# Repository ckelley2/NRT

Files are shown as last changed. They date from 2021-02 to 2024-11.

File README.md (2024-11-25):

# NRT Design and Testing Documentation

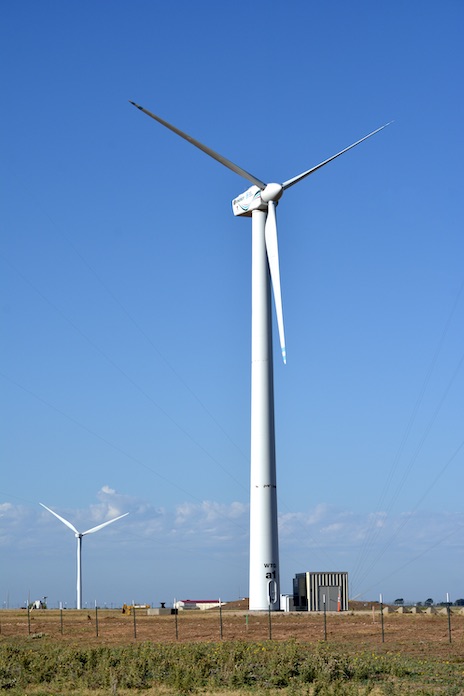
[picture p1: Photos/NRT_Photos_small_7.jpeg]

- National Rotor Testbed design documentation is contained in this repository
- [Field experiment](https://www.osti.gov/servlets/purl/1489535) is ongoing at Sandia/DOE SWiFT Facility, Lubbock, Texas
- Aerodynamic and instrumentation design by Sandia 
- Final structural design and manufacturing drawings were provided by Wetzel Wind Energy Services
- Oakridge National Laboratory 3D printed the NRT blade mold
- TPI Composites manufactured 4 NRT Blades
- Structural testing conducted at NREL

# Purpose
- To conduct wind turbine wake experiments relevant to megawatt scale turbines
- To be an open, well-documented, and highly instrumented wind turbine rotor design for model validation
- To demonstrate new blade technology

# [Aeroelastic Model](FAST_v7/)
- Modelled in [FAST version 7](https://www.nrel.gov/wind/nwtc/fastv7.html)
- Blade aerodynamics including chord, twist, and airfoil locations in aerodyn file [NRT_AD.ipt](FAST_v7/NRT_AD.ipt)
- Blade structural properites including edge, flap, tension, and torsional stiffness, mass moments of inertia, and mass distribution in each blade file [NRT_Blade1_as_built_balanced.dat](FAST_v7/NRT_Blade1_as_built_balanced.dat), [NRT_Blade2_as_built_balanced.dat](FAST_v7/NRT_Blade2_as_built_balanced.dat), [NRT_Blade3_as_built_balanced.dat](FAST_v7/NRT_Blade3_as_built_balanced.dat)
- Blade mass distribution updated to include ballast in balance boxes of each blade
- Airfoil lift, drag, and moment data from experimental wind tunnel testing by Somers
- Model will continue to be updated during ongoing NRT experiment
- Simple controller model, variable speed, variable pitch
- Please contact us for a detailed simulink model of the turbine controller
- Plotting scripts in matlab require [txt2mat](https://www.mathworks.com/matlabcentral/fileexchange/18430-txt2mat)

# Blade Instrumentation 
- Strain gages:
  - Micron Optics Fiber Optic OS3200
  - Spaced 45 degrees at root, high/low pressure side outboard
  - calibrated to measure aerodynamic bending moment
- Accelerometers:
  - Silicon Designs 2470
- Blade Temperature:
  - Micron Optics Fiber Optic OS4300
  - to compensate for thermal strain
- All three blades have same sensors  
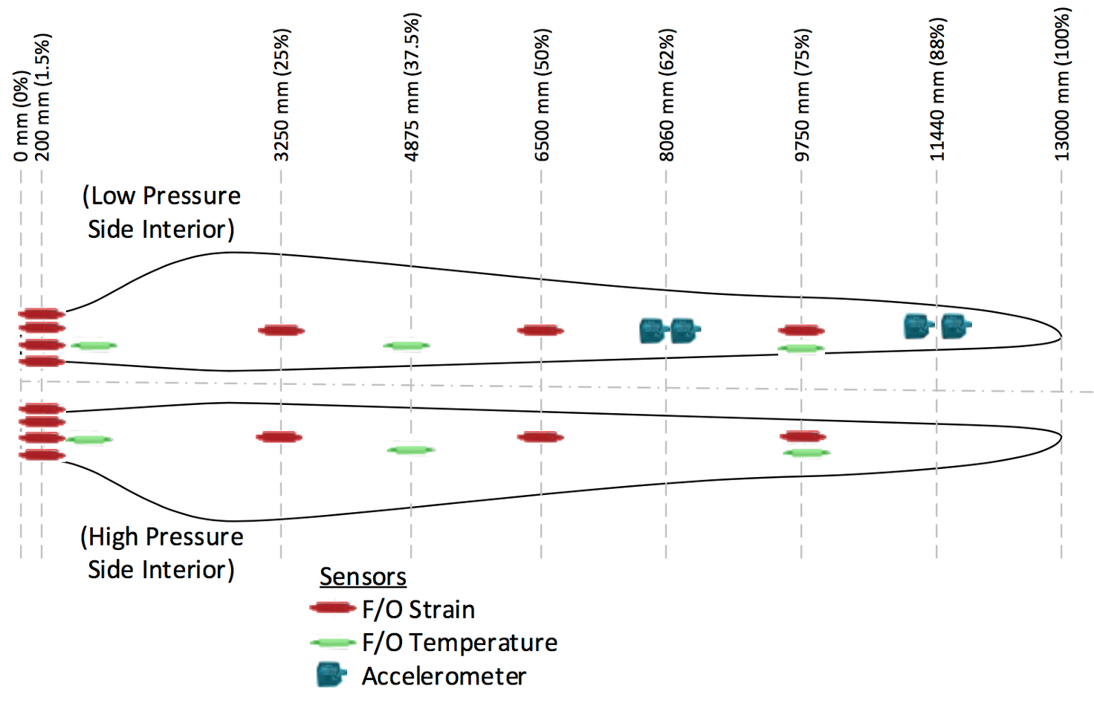
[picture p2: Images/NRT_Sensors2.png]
  

# Blade Properties
- Length: 13 m
- Blade Mass: 551 kg per blade, including balance box ballast 
- Blade Center of Gravity: 4.04 m from root
- Construction: Fiberglass spar and skin
- Surface Roughness (Painted, clean): Ra = 0.45 𝜇m (17 𝜇in), Rz = 2.57 𝜇m (101 𝜇in)

# Regions of Operation
- Region 2:   4-6.9 m/s, 25.9-43.6 rpm, TSR = 9
- Region 2.5: 6.9-11.4 m/s, 43.6-43.9 rpm
- Region 3:   11.4-20 m/s, 43.9 rpm   
  
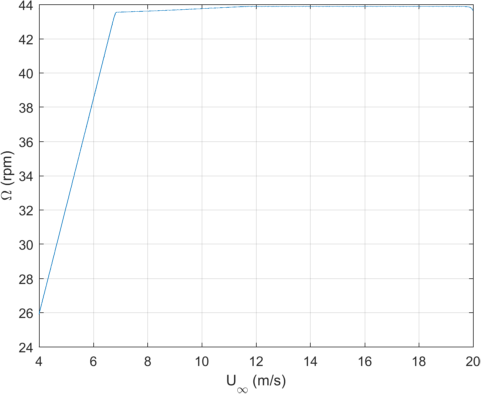
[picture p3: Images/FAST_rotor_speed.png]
 

# Aerodynamic Design
- [Technical Report](https://www.osti.gov/biblio/1346410-aerodynamic-design-national-rotor-testbed)
- Create scaled wake of GE 1.5sle (GE37c blade) by having the same axial induction, $a$, and dimensionless circulation, $\Gamma'$,  across the rotor normalized radius, $\frac{r}{R}$, in region 2
- NRT and GE rotor also have equal thrust coefficient $C_T$ and tip-speed-ratio $\lambda = 9$ in region 2
- [S825](https://www.nrel.gov/docs/fy05osti/36346.pdf) airfoil across outer 50% of rotor span
- [S814](https://wind.nrel.gov/airfoils/documents/S814_WTtest_OCR.pdf) airfoil at maximum chord, c = 1.5 m
- Airfoils operate at a lift coefficient of 0.6 in region 2  
- Overview of functional scaling [(.pdf)](Documents/NRT_Functional_Scaling.pdf)

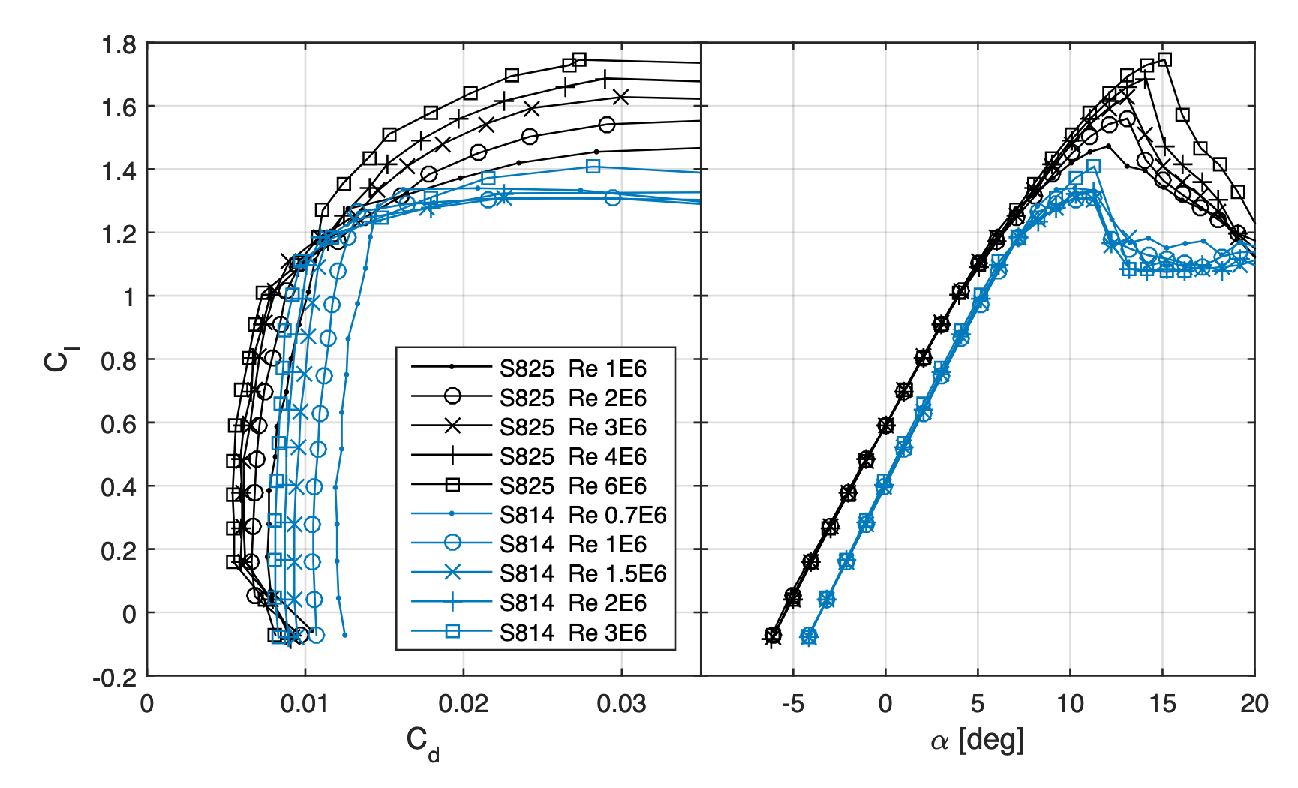
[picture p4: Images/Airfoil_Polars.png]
 <br/>

# Structural Design
- [Mass, Stiffness, and Modal Analysis Report (.pdf)](Structure/WEI%20169.03.06.001-B-Sandia%2013m%20Blade_Structural%20Analysis%20Summary.pdf)
- [Beam Properties (.xlsx)](Structure/169.05.02.001-B-Aero+Structure%20Design%20Summary.xlsx?raw=true)
- [Material Properties and Standards (.xlsx)](Structure/169.03.03.001-A_Sandia_13.0m%20Blade%20Materials%20and%20Test%20Standards_2016-02-....xlsx?raw=true)
- [3D CAD Models](Structure/3D%20CAD%20Models)
- [Manufacturing Drawings](Structure/Design%20Drawings)
- Note, the root plane was cut to add 0.5° of forward sweep to reduce nose down pitching moment about the blade pitch axis
- Initial structural design [report](https://www.osti.gov/biblio/1225852-nrt-rotor-structural-aeroelastic-analysis-preliminary-design-review) at Sandia in 2015, superseded by Wetzel structural design

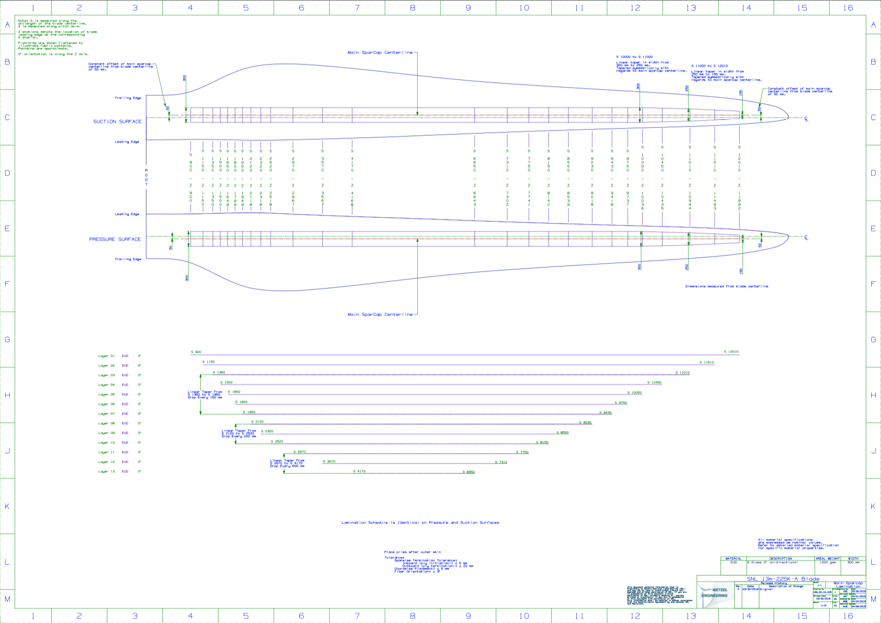
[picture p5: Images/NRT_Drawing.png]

  
# Static Blade Testing
- Conducted at NREL Structural Testing Lab
- [Test Report (.pdf)](Documents/NRT%20Blade%20Laboratory%20Structural%20Test%20Report.pdf)
- Proof Tests:
  - maximum and minimum edge loads
  - maximum and minimum flap loads
  - fatigue test in flap direction
  - ultimate flap load to failure
    
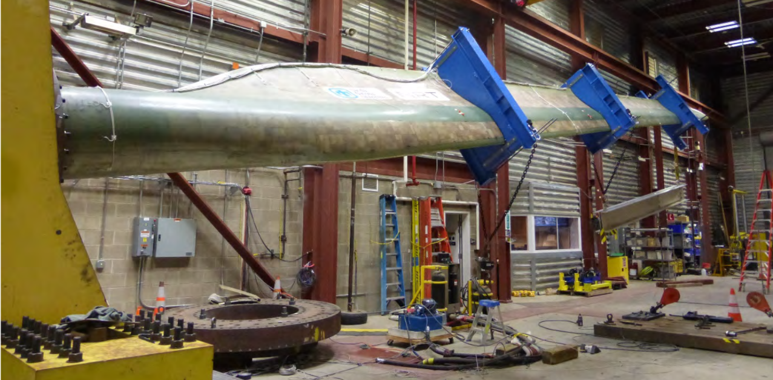
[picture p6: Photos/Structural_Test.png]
  

# Field Test
- Verify blade loading distribution creates scaled wake of GE 1.5 sle 
- Fine tune pitch setting to create scaled wake
- Fine tune torque constant to achieve $\lambda=9$
- See [technical report](https://www.osti.gov/servlets/purl/1489535) for description of tuning process
- Blade bending moment coefficients to achieve scaled wake (at reference air density of 1.225 $\textrm{kg/m}^3$) are as follows for discreet strain gage locations in thrust and edge directions
- Wake Management demonstration showing a combination of yaw, induction, and [dynamic induction](https://arc.aiaa.org/doi/abs/10.2514/6.2021-1182) control
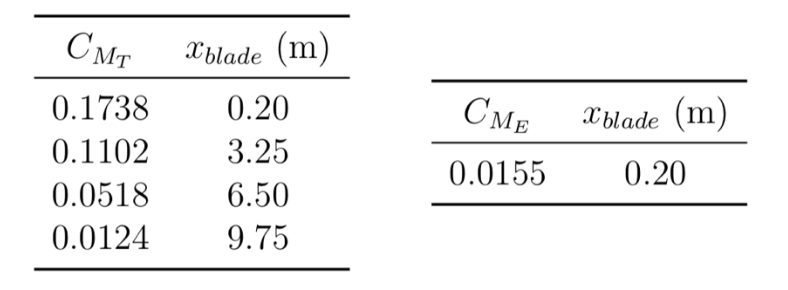
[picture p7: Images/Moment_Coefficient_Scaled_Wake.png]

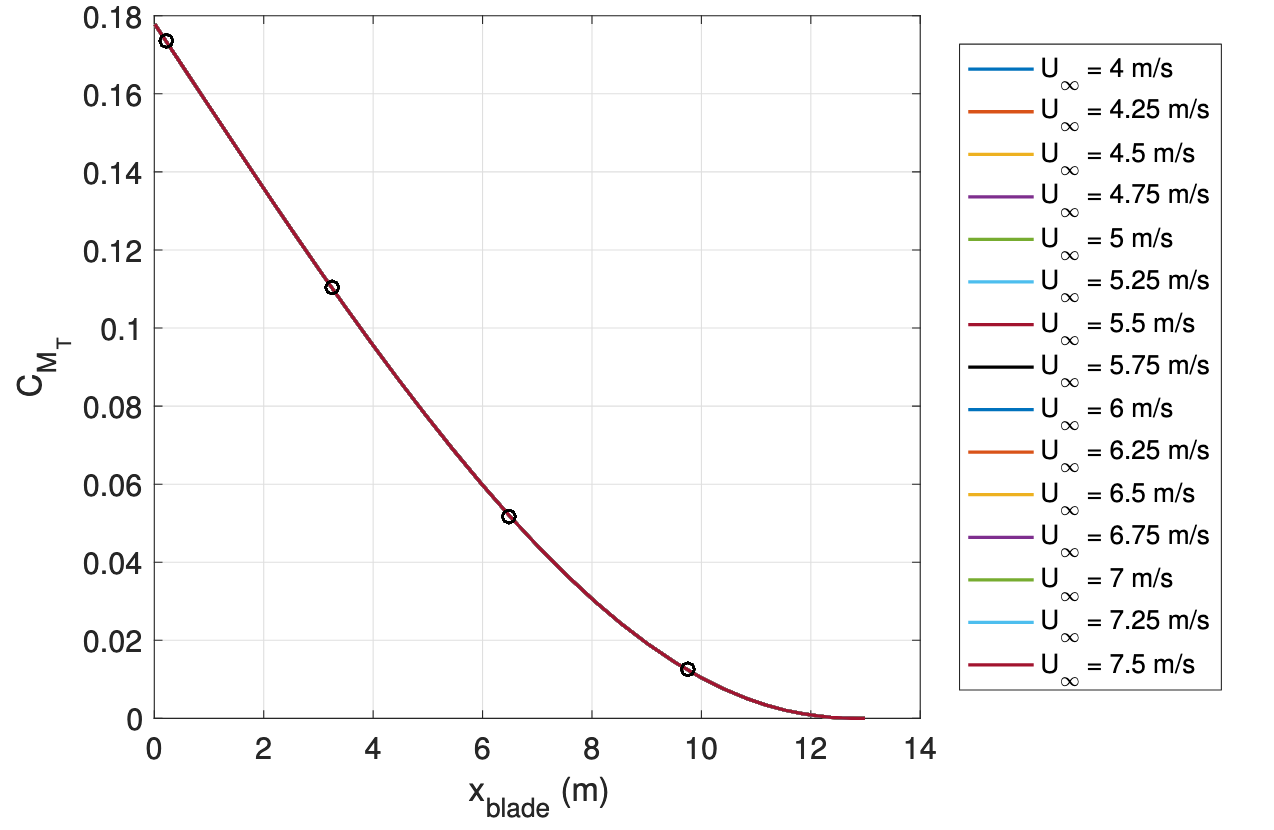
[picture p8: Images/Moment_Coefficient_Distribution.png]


# SWiFT Site Documentation
- [SWiFT Site Overview](https://energy.sandia.gov/programs/renewable-energy/wind-power/wind_plant_opt/)
- [Wind Resource Assessment and Characterization](https://www.osti.gov/biblio/1237403-swift-site-atmospheric-characterization)

# Point of Contact
Chris Kelley  
clkell@sandia.gov

# References
C. Kelley, "Aerodynamic Design of the National Rotor Testbed," Sandia National Laboratories Technical Report, [SAND2015-8989](https://www.osti.gov/biblio/1346410-aerodynamic-design-national-rotor-testbed).  

C. Kelley, B. Naughton, "NRT Design Verification Test Plan," Sandia National Laboratories Technical Report, [SAND2018-14254](https://www.osti.gov/biblio/1346410-aerodynamic-design-national-rotor-testbed).  

C. Kelley, "National Rotor Testbed Overview for DOE Science Panel," Project Presentation, [SAND2017-4446PE](https://www.osti.gov/servlets/purl/1431697).

B. Ennis, J. Paquette, "NRT Rotor Structural/Aeroelastic Analysis for the Preliminary Design Review," Sandia National Laboratories Technical Report, [SAND2015-9358](https://www.osti.gov/biblio/1225852-nrt-rotor-structural-aeroelastic-analysis-preliminary-design-review)

# Copyright
Copyright 2020 National Technology & Engineering Solutions of Sandia, 
LLC (NTESS). Under the terms of Contract DE-NA0003525 with NTESS, the U.S. 
Government retains certain rights.
 
NRT design documentation is distributed in the hope that it will be useful, but without any 
warranty; without even the implied warranty of merchantability or fitness for a 
particular purpose.

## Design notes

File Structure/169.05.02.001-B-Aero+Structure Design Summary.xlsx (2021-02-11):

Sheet: COVER
 | Sandia 13m BLADE AERO-STRUCTURE DESIGN SUMMARY
 | Document Number: |  | 169.05.02.001
 | Document Release Version: |  | B
 | Release Date: |  | 2016-04-26
 | Client: |  | Sandia National Laboratories
 | PO Number: |  | 42389
 | Agreement Date: |  | 1322724 Rev.11
 | Task: |  | 3B. Detail Structural Design
 | Client POC: |  | Josh Paquette
 | Consultant PI: |  | Dr. Kyle K. Wetzel
 | Document Approval |  |  | Name | Date
 | Curent Release Author: |  |  | Alejandra S. Escalera | 2016-04-21
 |  |  |  | (ase@WetzelEngineering.com)
 | Current Release Checked By: |  |  | Alex R. Tran | 2016-04-22
 | Current Release Approved By: |  |  | Kyle K. Wetzek | 2016-Apr-23
 | REVISION HISTORY
 | Version | Release Date | Author |  | Changes
 | A | 2016-03-09 | Alejandra S. Escalera |  | Original
 | B | 2016-04-22 | Alejandra S. Escalera |  | Updated after completion of task 3.C
Wetzel Engineering, Inc. ● 3914 Gattis School Road, Suite 103 ● Round Rock, TX 78664 ● U.S.A. 512-989-9194 ● info@WetzelEngineering.com ● www.WetzelEngineering.com
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

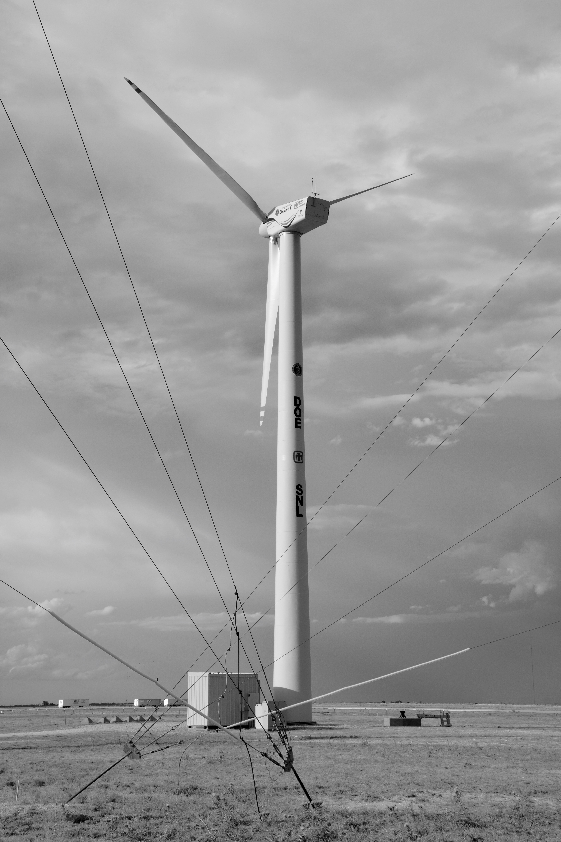
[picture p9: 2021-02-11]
Photos/NRT_Photos_4.jpeg

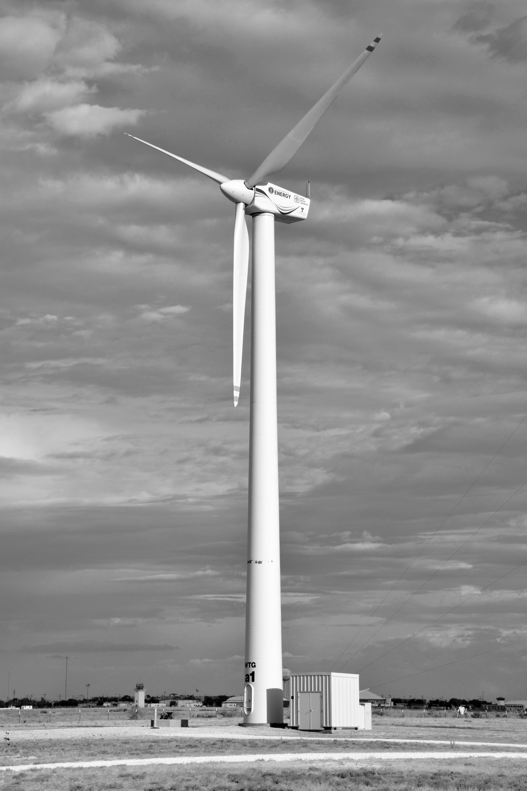
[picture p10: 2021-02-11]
Photos/NRT_Photos_2.jpeg

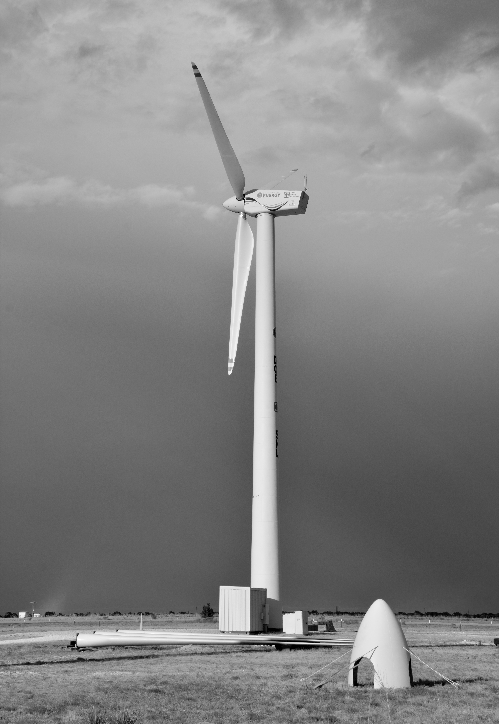
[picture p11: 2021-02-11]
Photos/NRT_Photos_5.jpeg

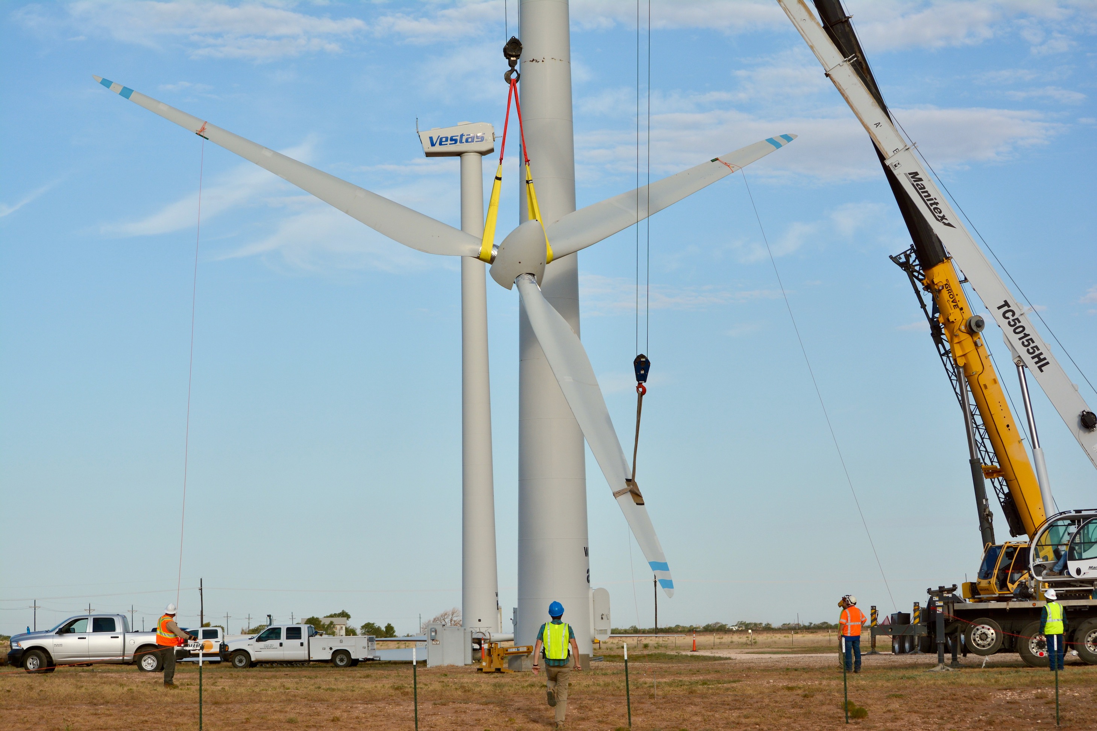
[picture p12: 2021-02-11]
Photos/NRT_Photos_small_1.jpeg

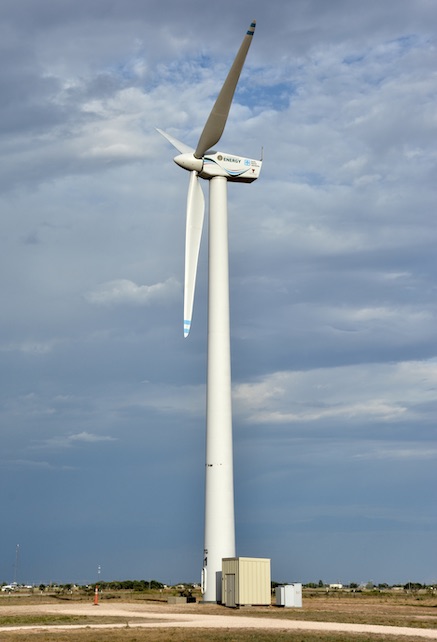
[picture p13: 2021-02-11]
Photos/NRT_Photos_small_3.jpeg

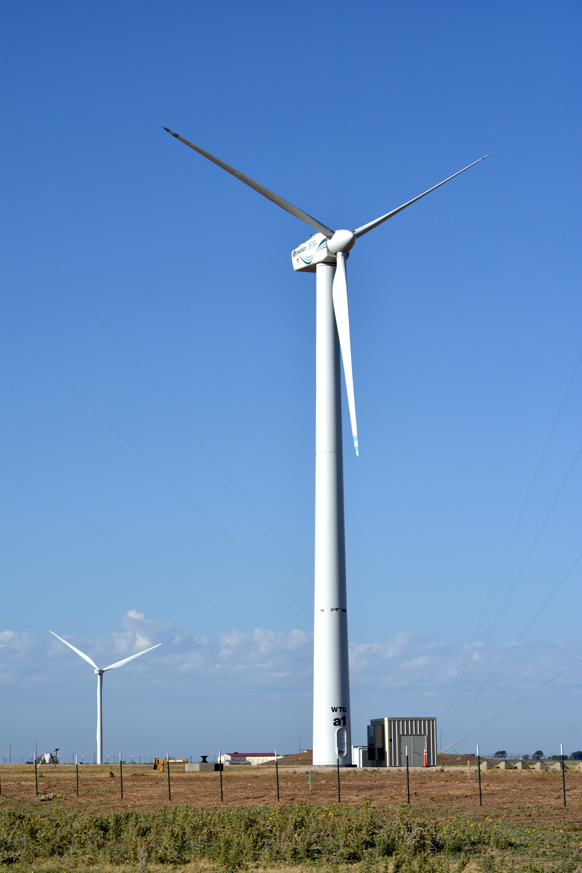
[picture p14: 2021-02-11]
Photos/NRT_Photos_7.jpeg

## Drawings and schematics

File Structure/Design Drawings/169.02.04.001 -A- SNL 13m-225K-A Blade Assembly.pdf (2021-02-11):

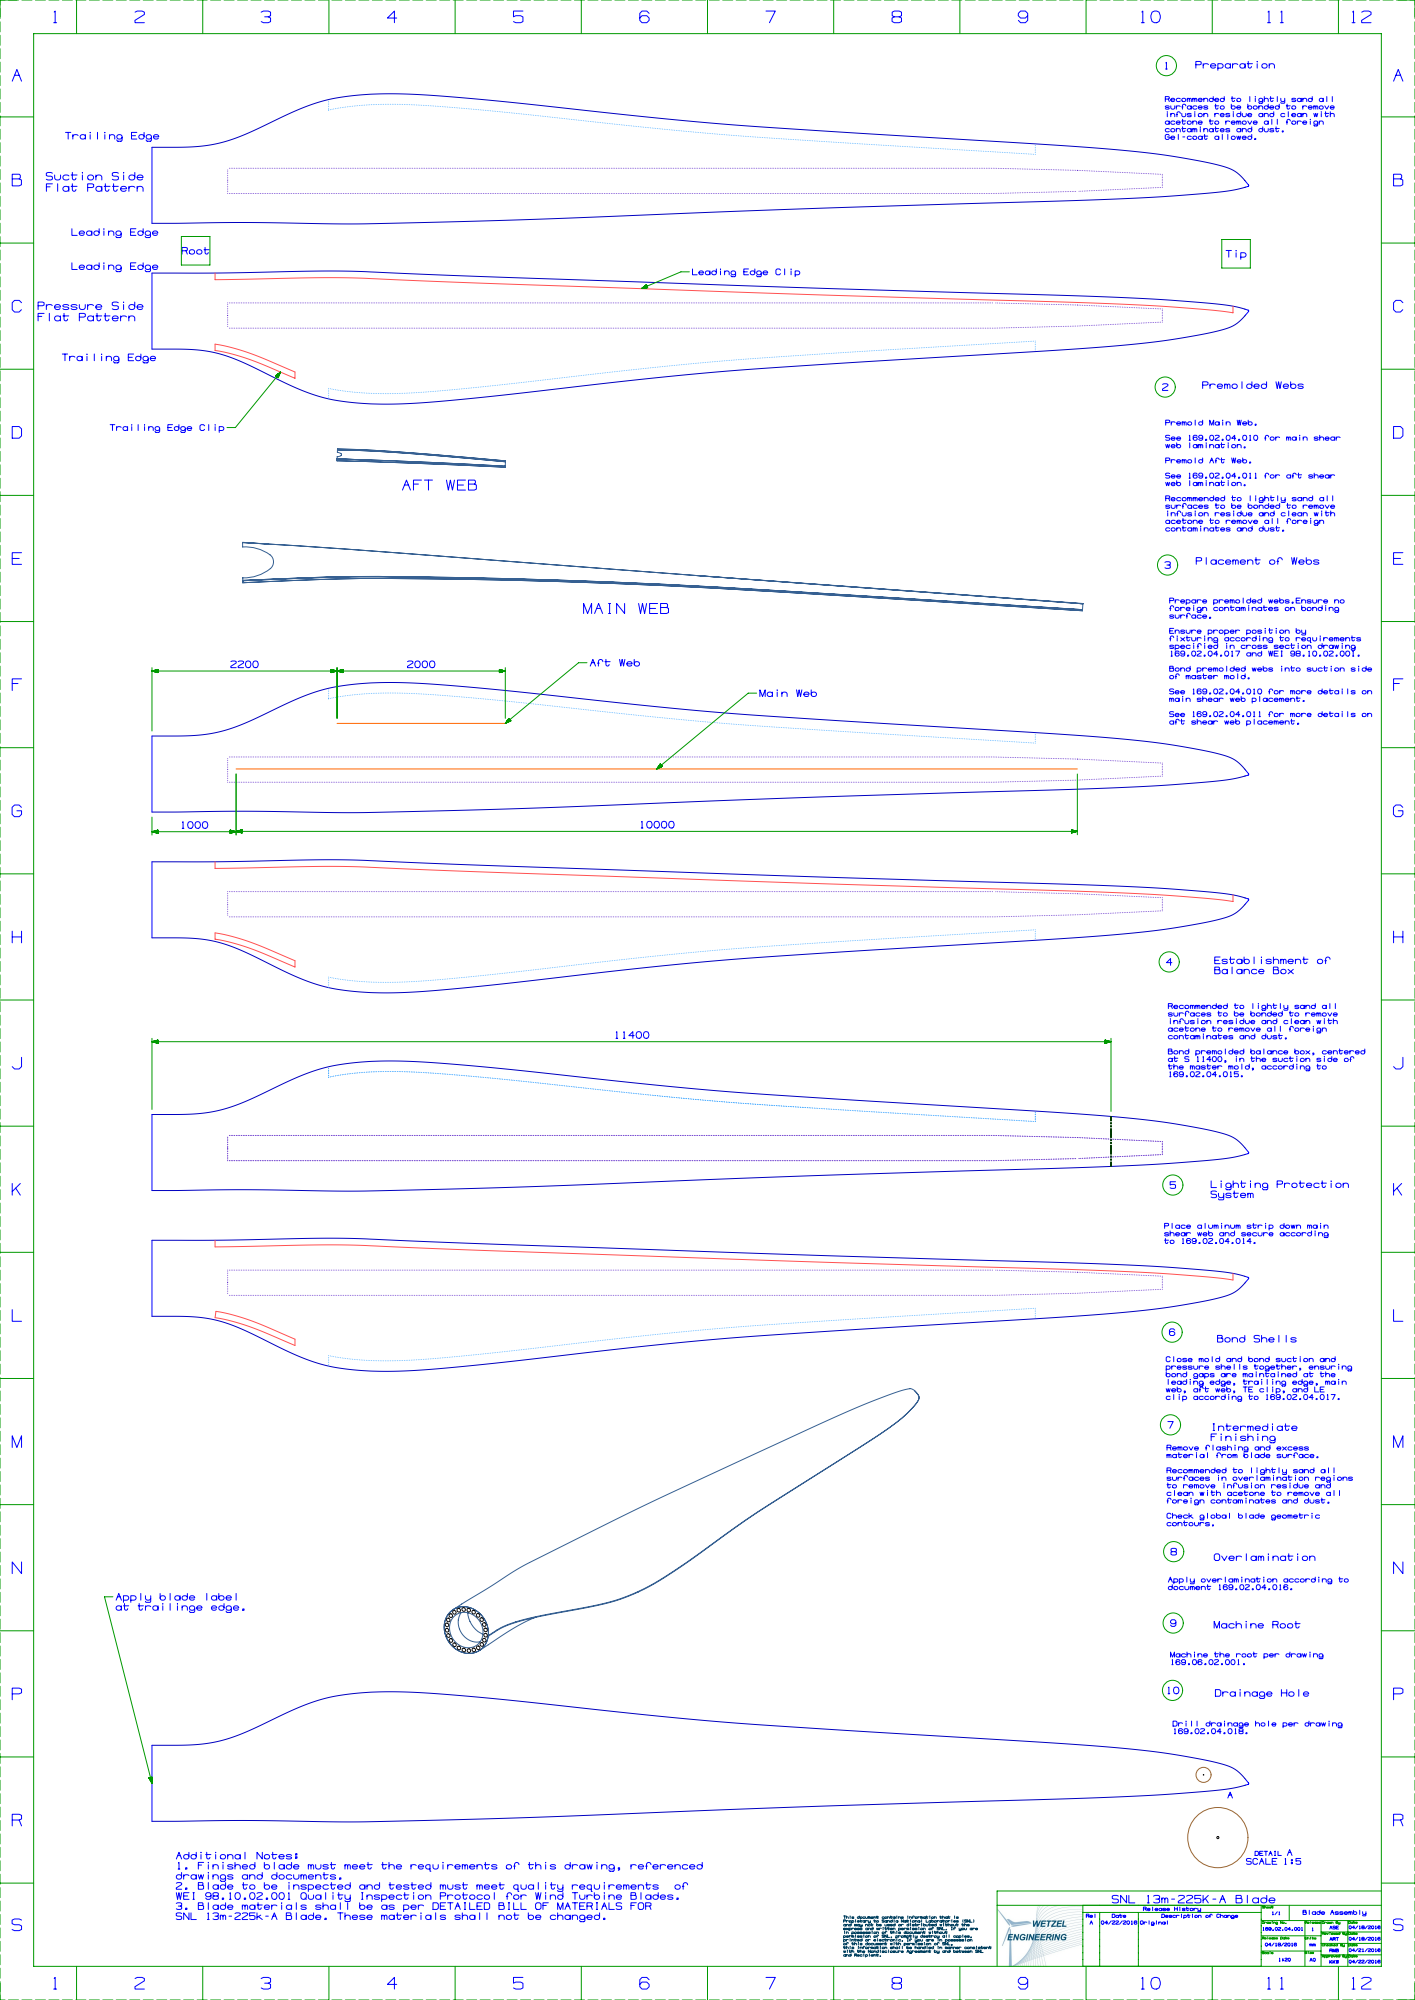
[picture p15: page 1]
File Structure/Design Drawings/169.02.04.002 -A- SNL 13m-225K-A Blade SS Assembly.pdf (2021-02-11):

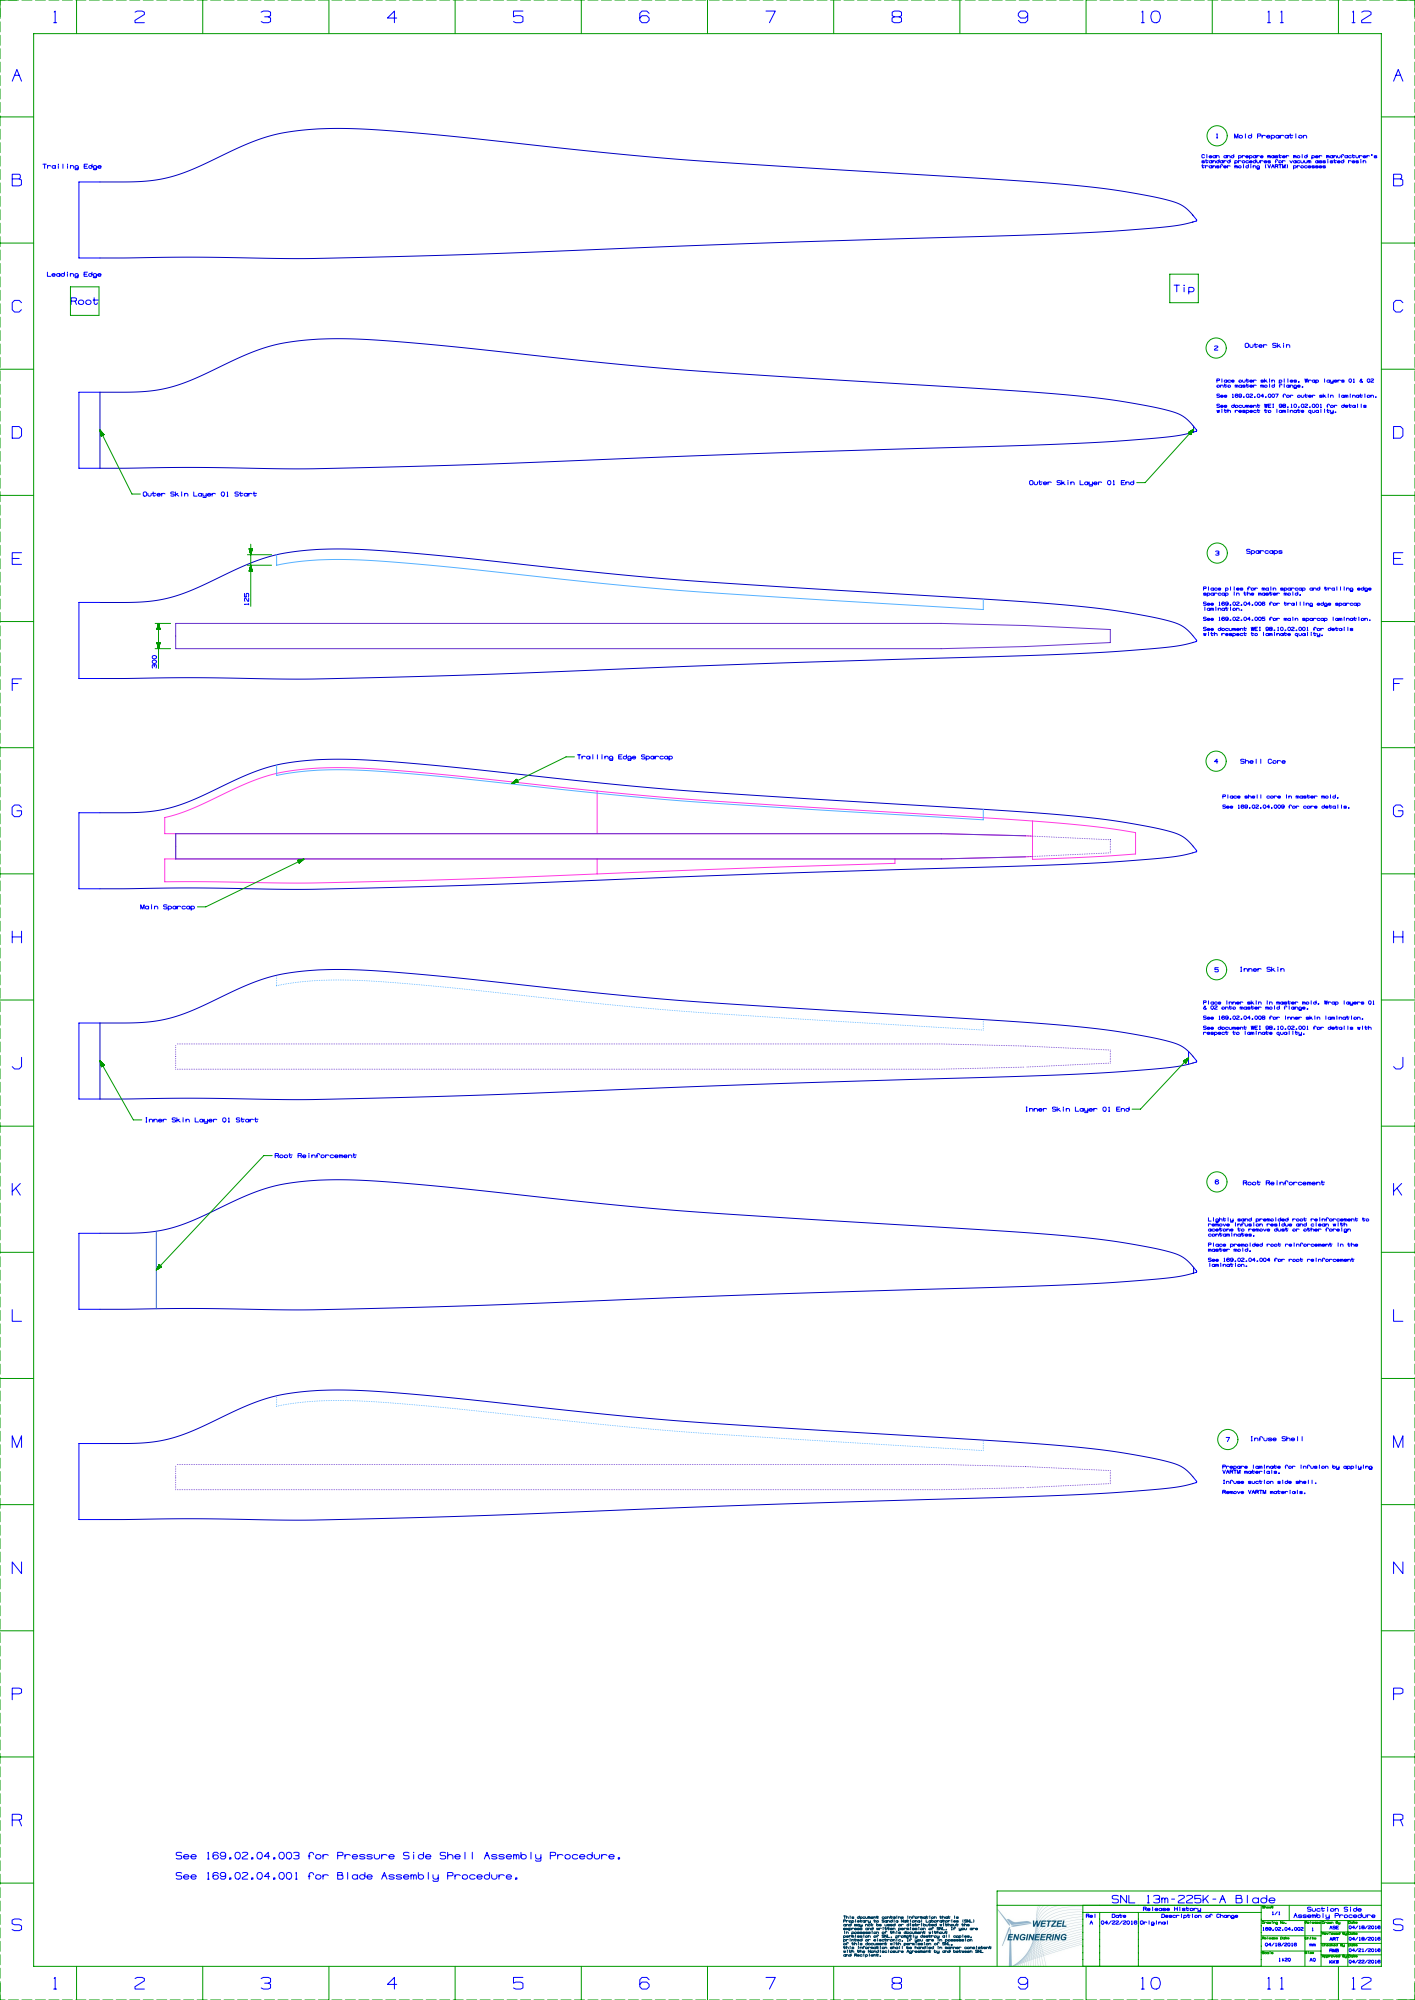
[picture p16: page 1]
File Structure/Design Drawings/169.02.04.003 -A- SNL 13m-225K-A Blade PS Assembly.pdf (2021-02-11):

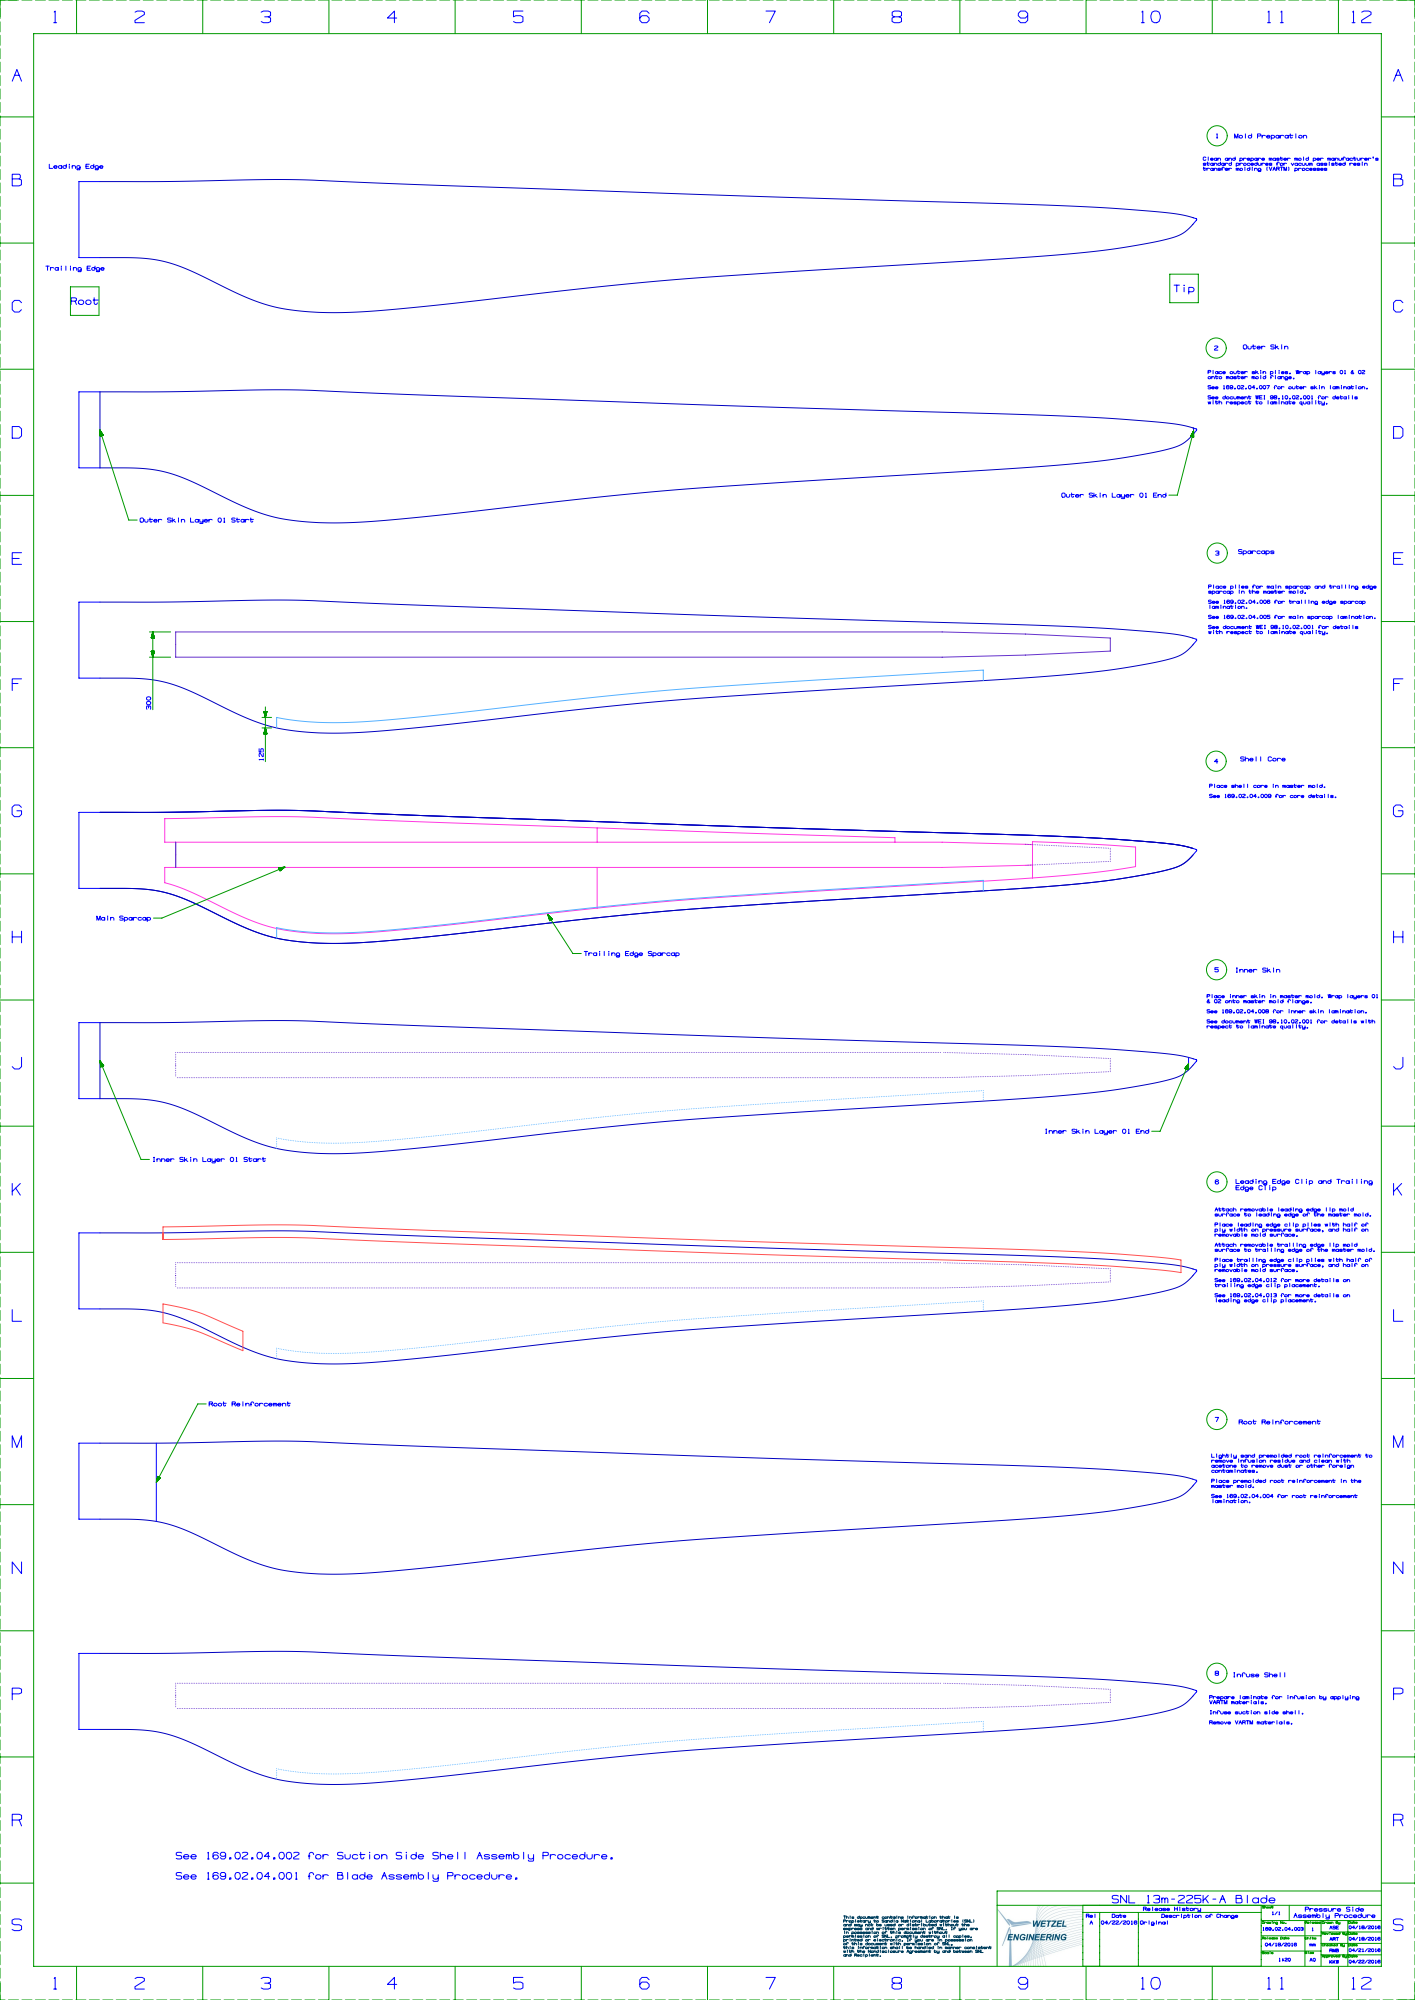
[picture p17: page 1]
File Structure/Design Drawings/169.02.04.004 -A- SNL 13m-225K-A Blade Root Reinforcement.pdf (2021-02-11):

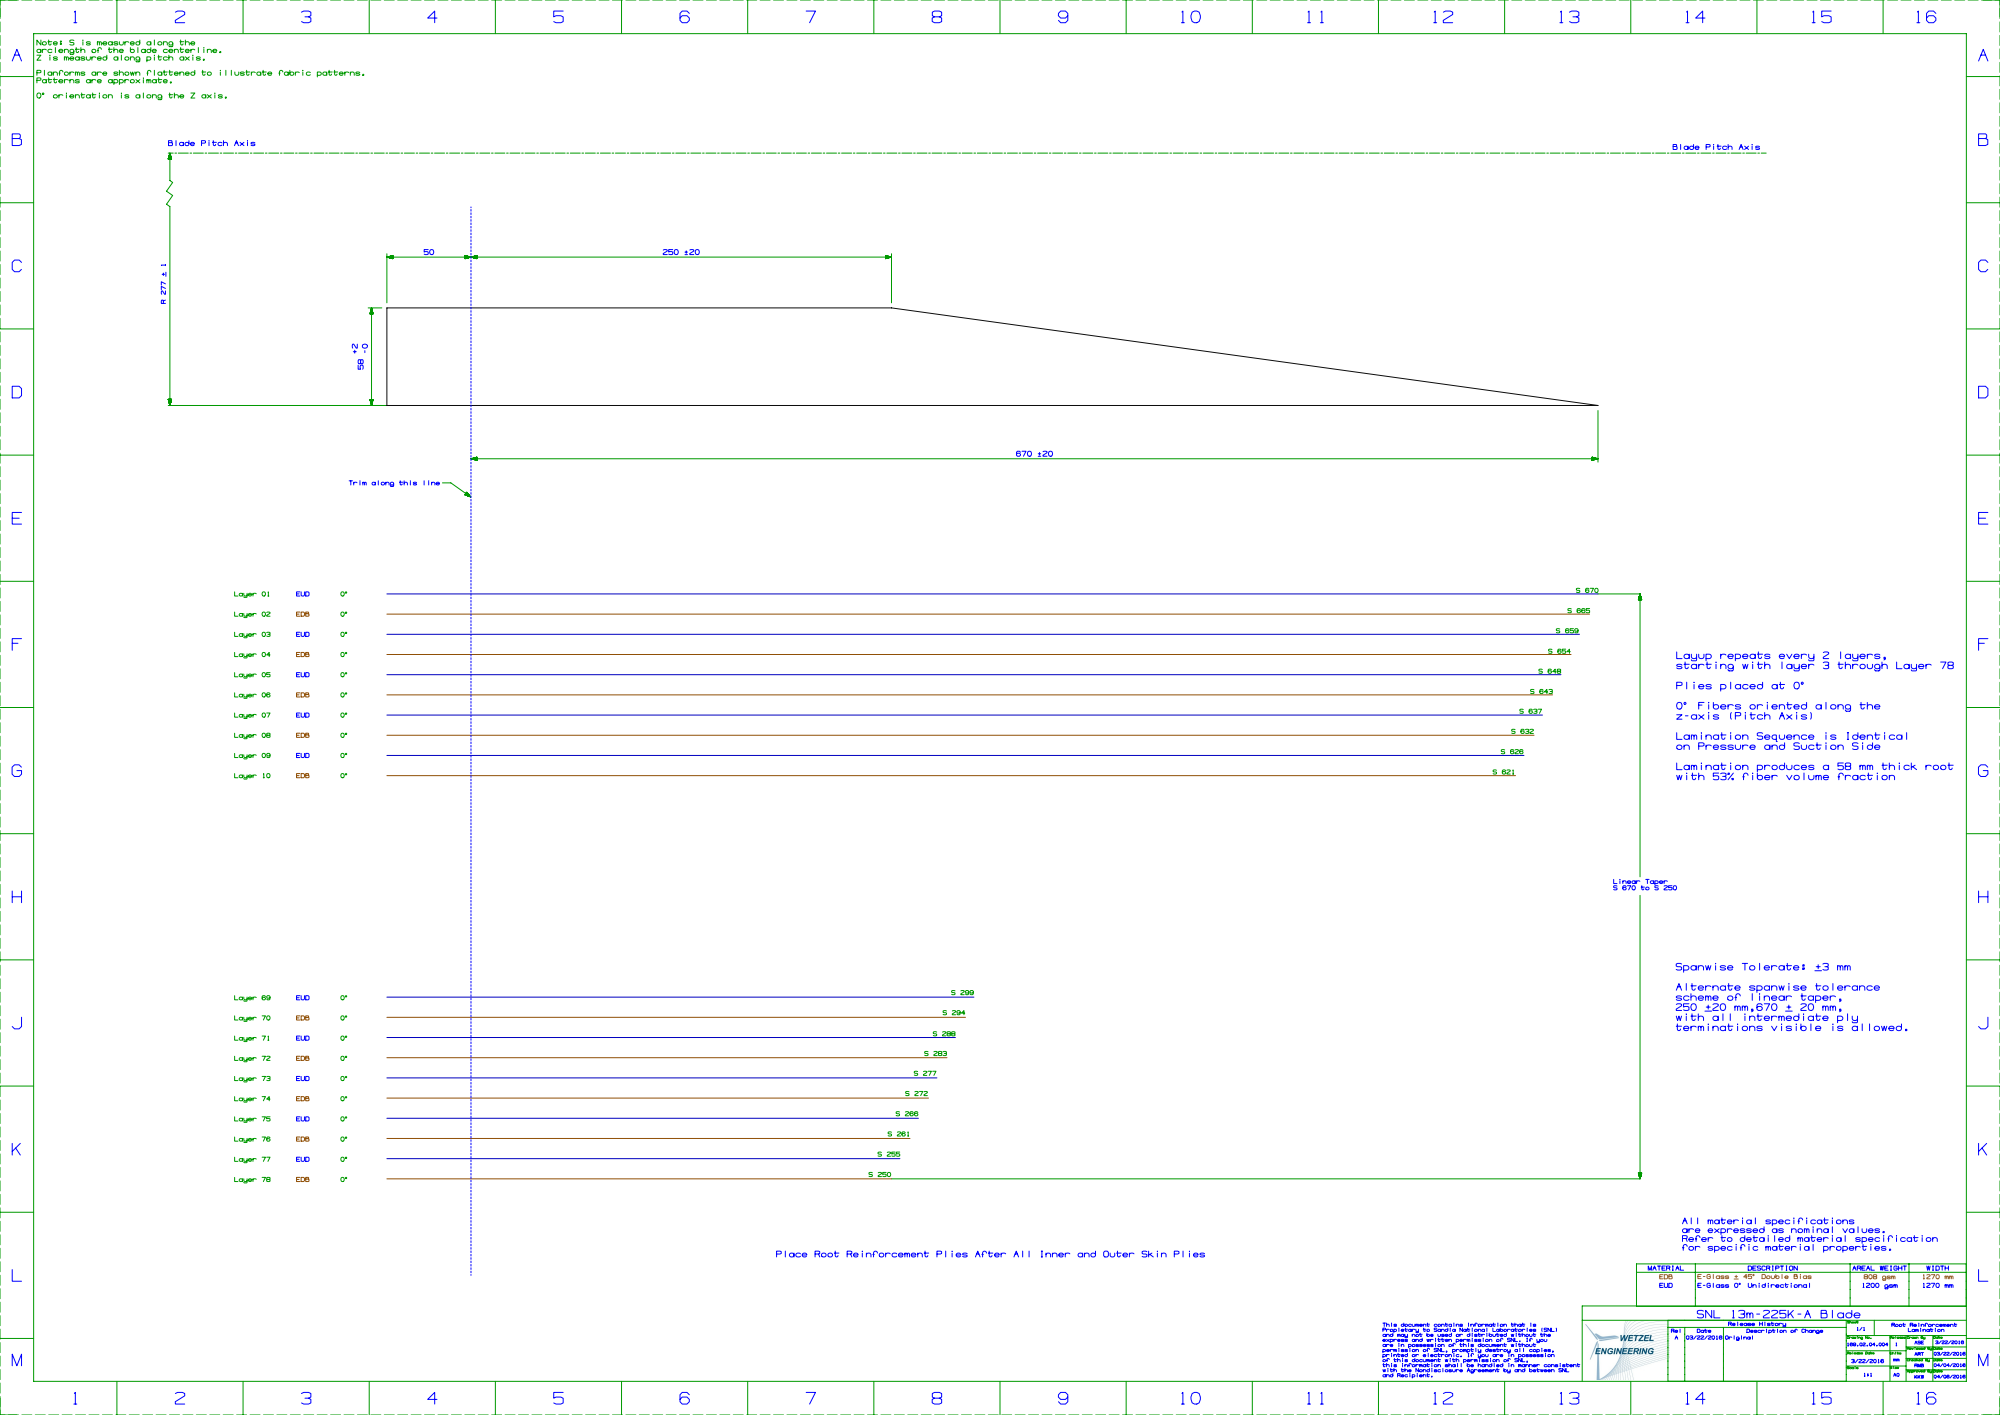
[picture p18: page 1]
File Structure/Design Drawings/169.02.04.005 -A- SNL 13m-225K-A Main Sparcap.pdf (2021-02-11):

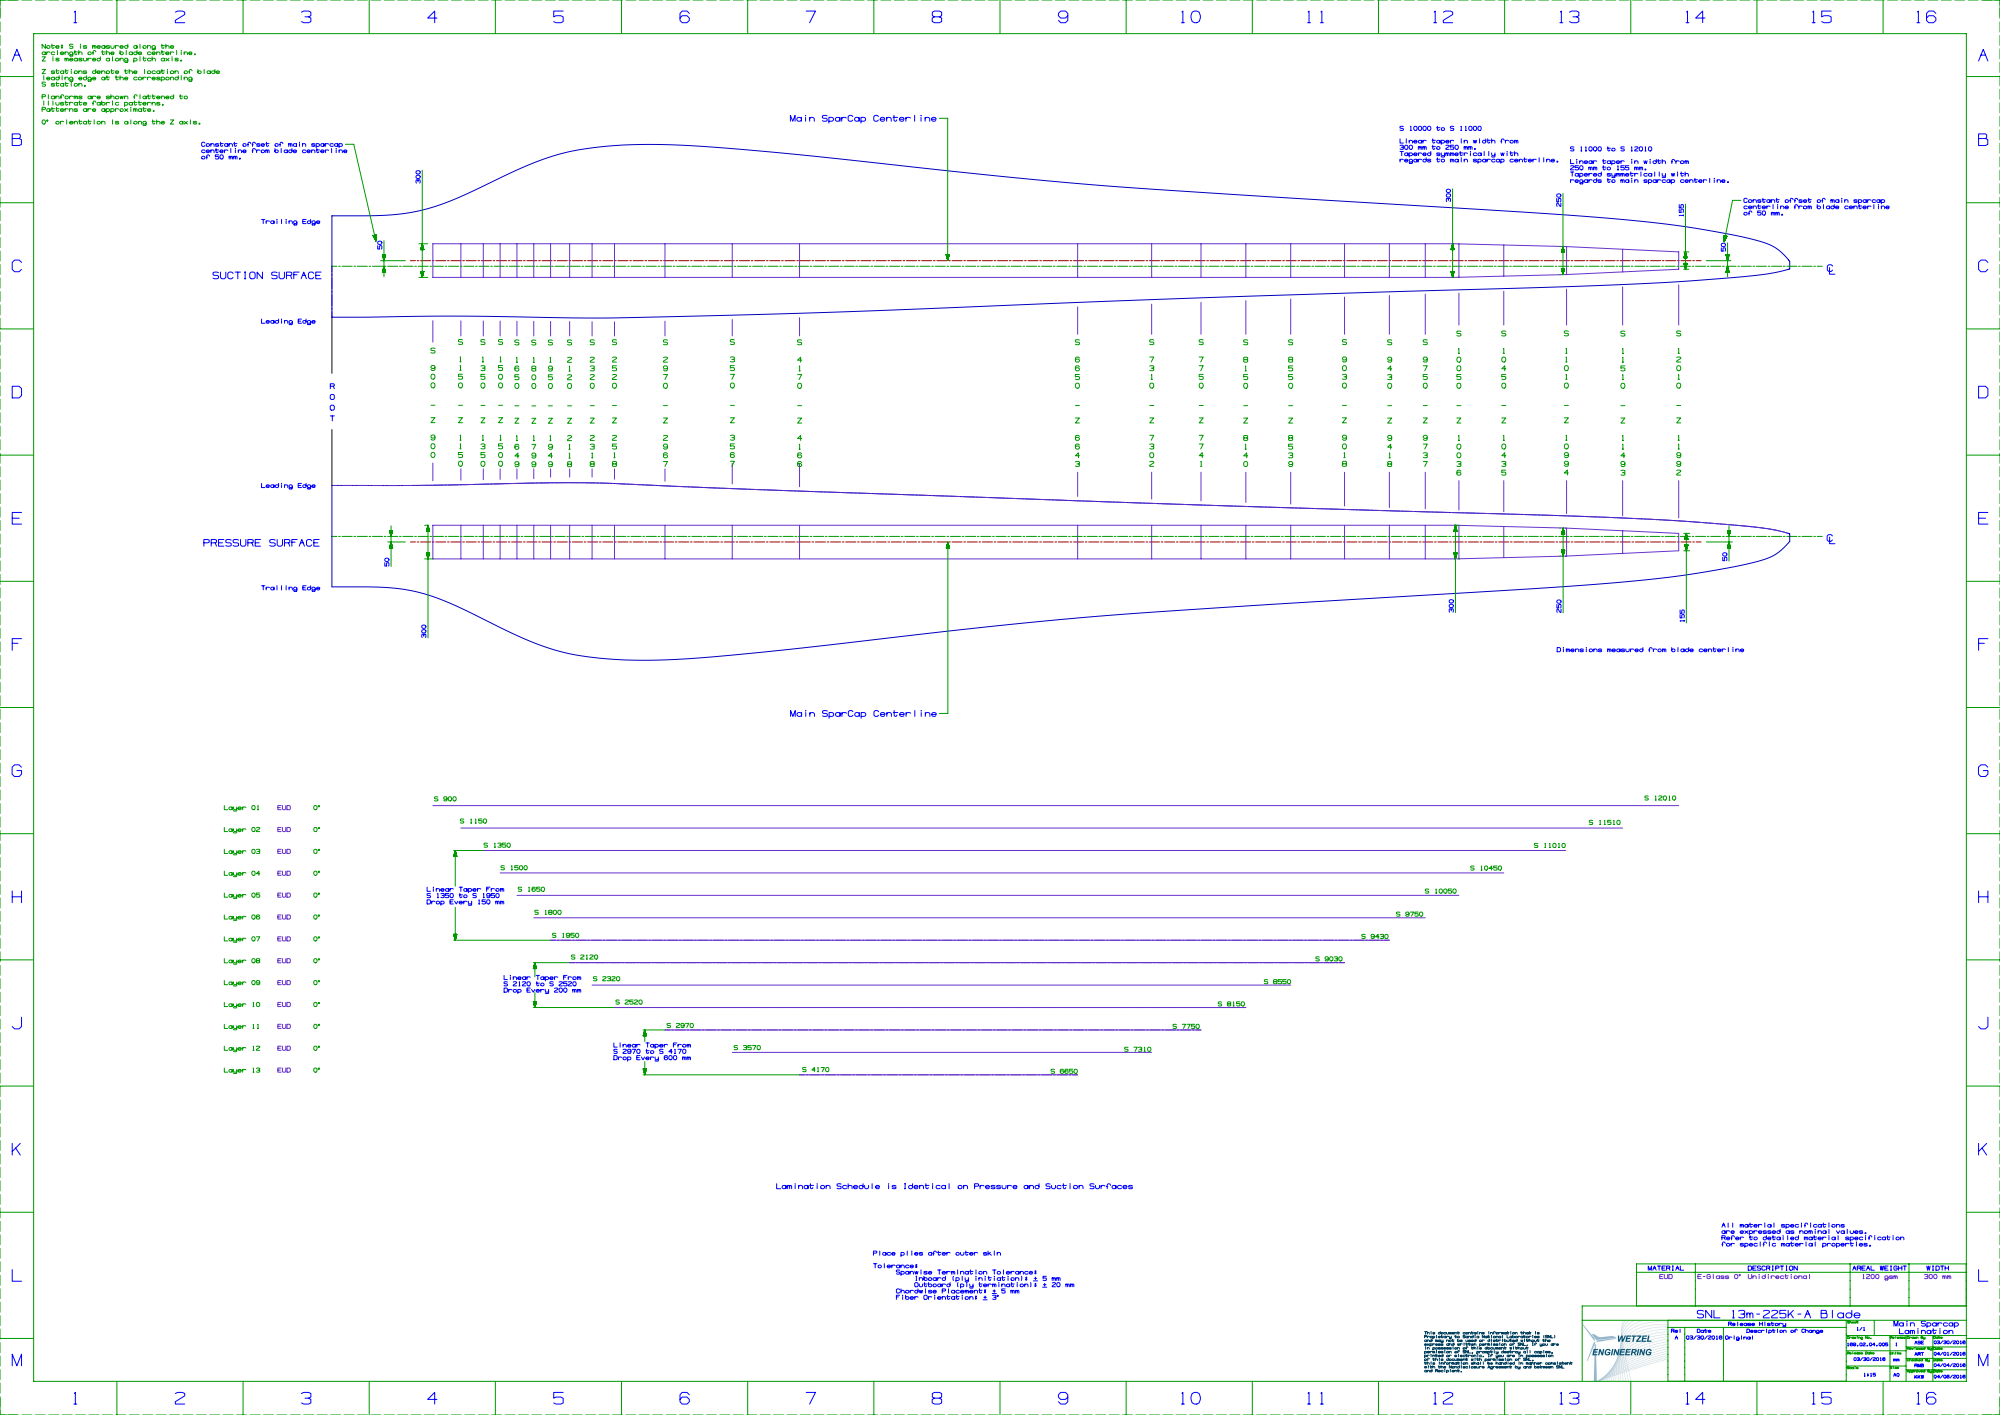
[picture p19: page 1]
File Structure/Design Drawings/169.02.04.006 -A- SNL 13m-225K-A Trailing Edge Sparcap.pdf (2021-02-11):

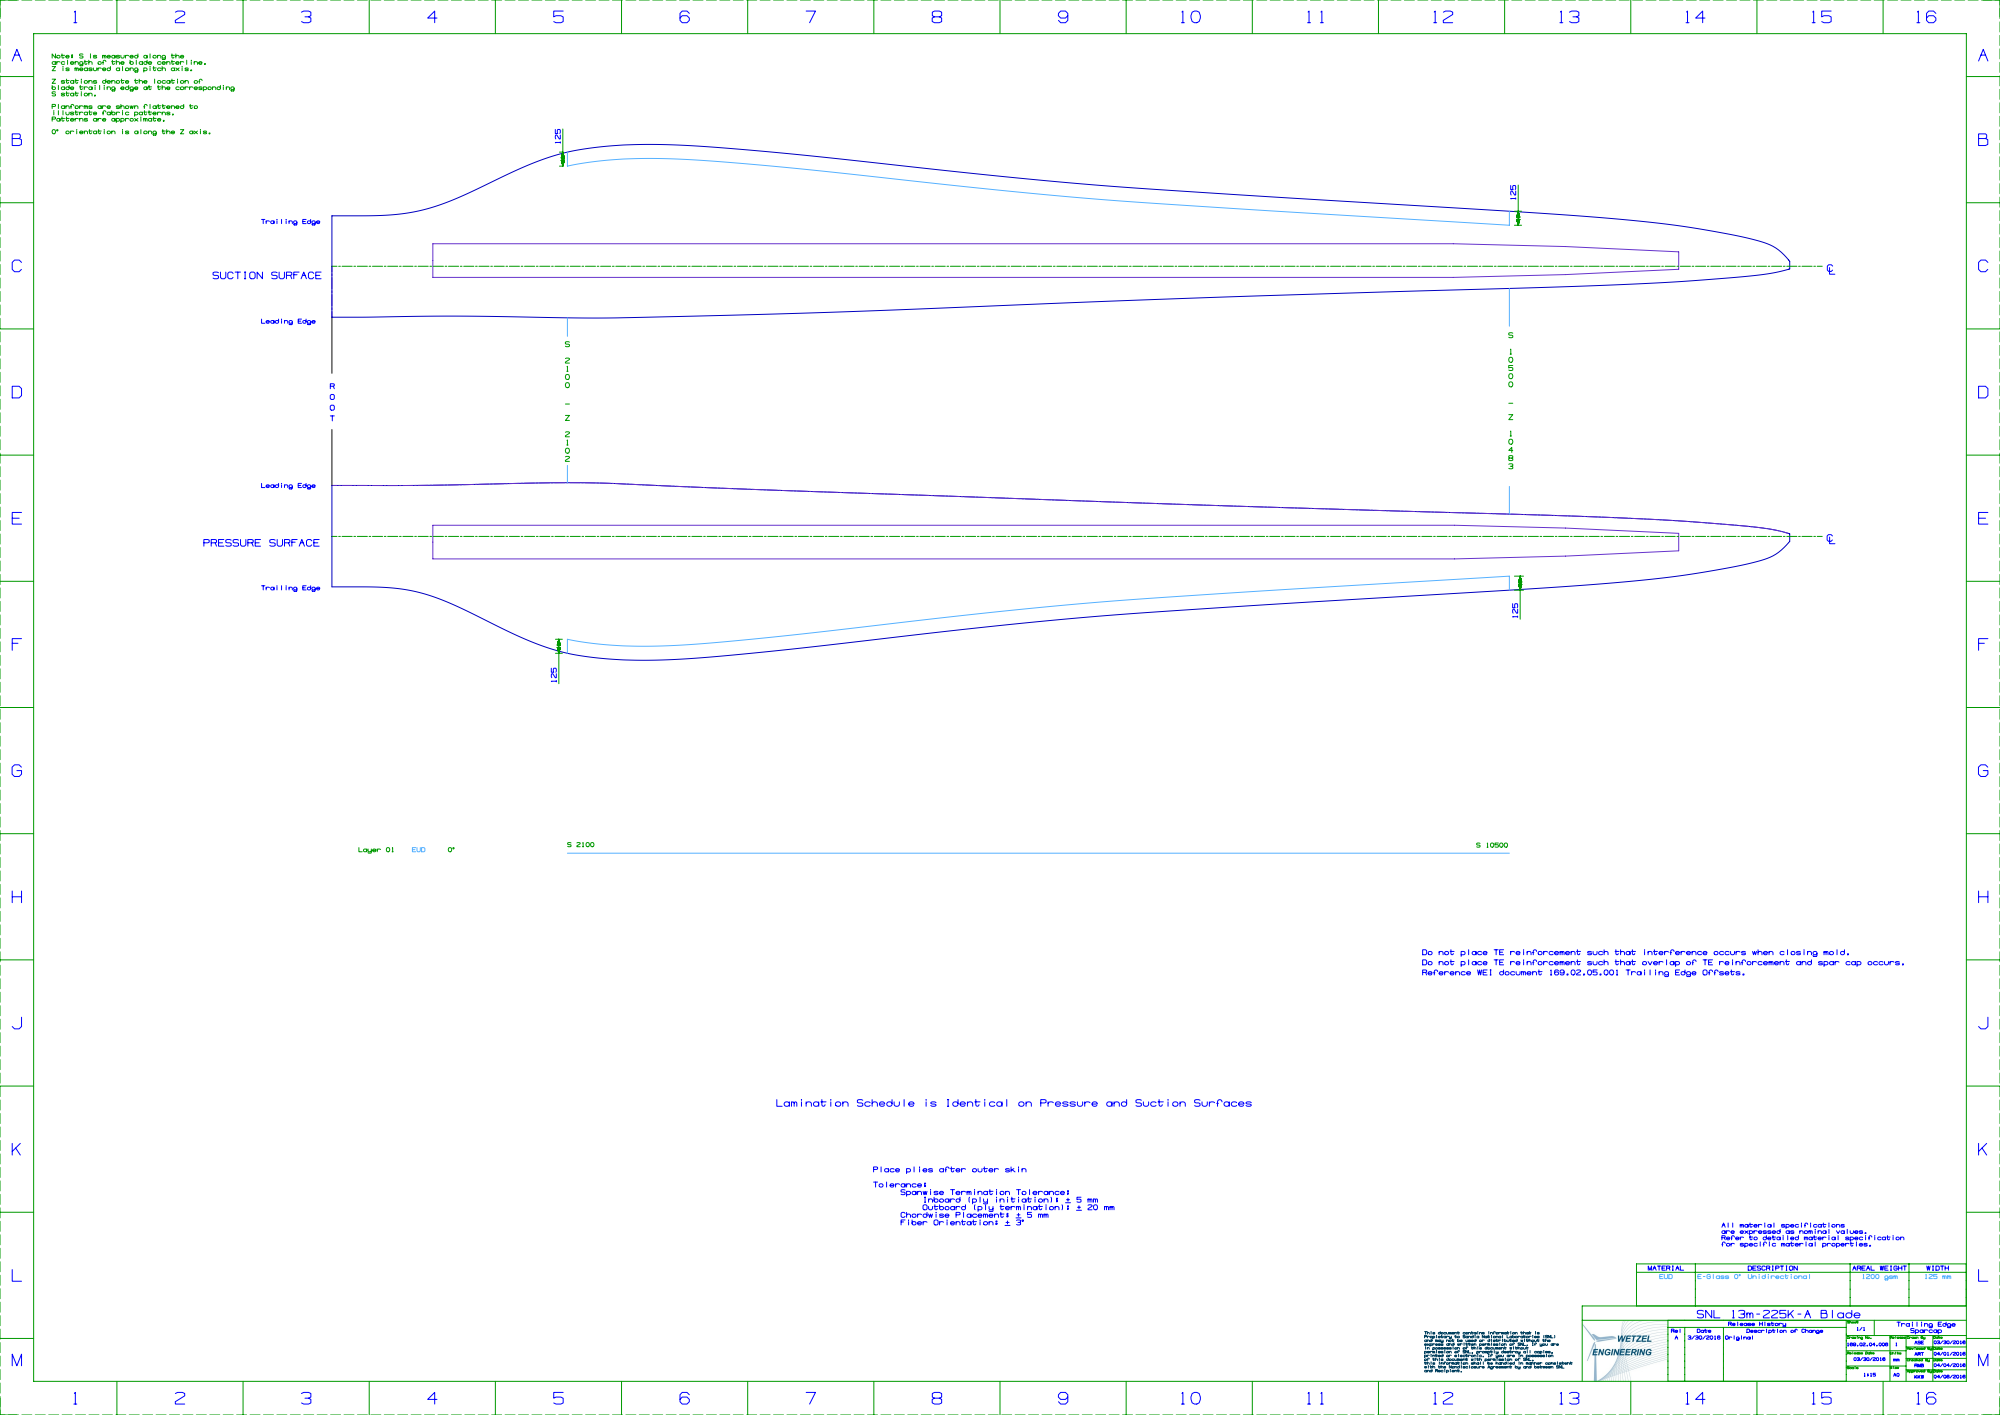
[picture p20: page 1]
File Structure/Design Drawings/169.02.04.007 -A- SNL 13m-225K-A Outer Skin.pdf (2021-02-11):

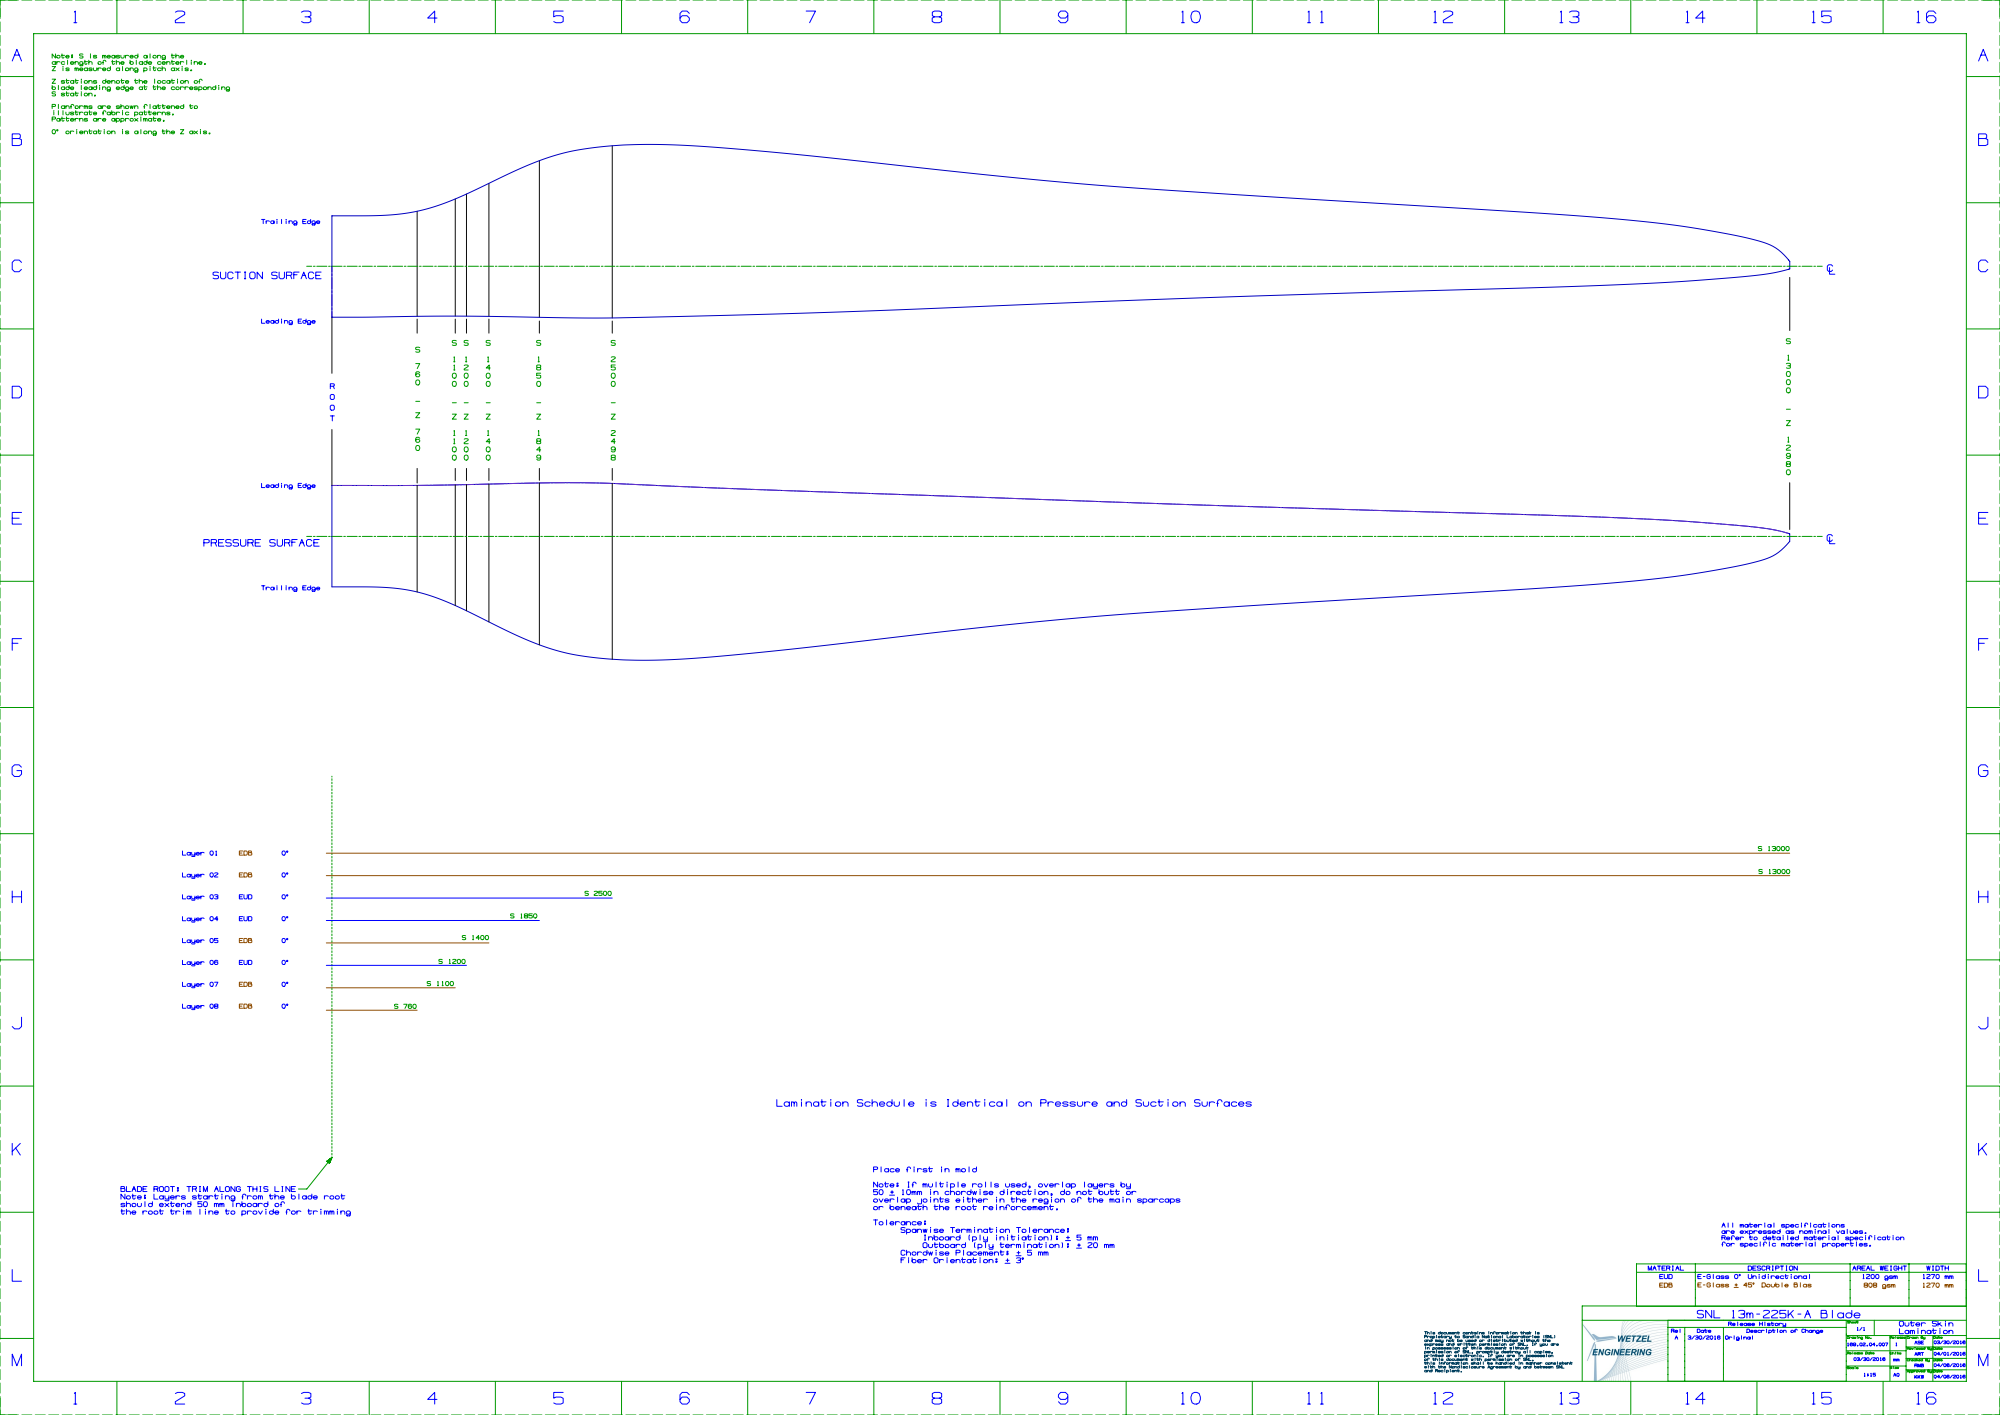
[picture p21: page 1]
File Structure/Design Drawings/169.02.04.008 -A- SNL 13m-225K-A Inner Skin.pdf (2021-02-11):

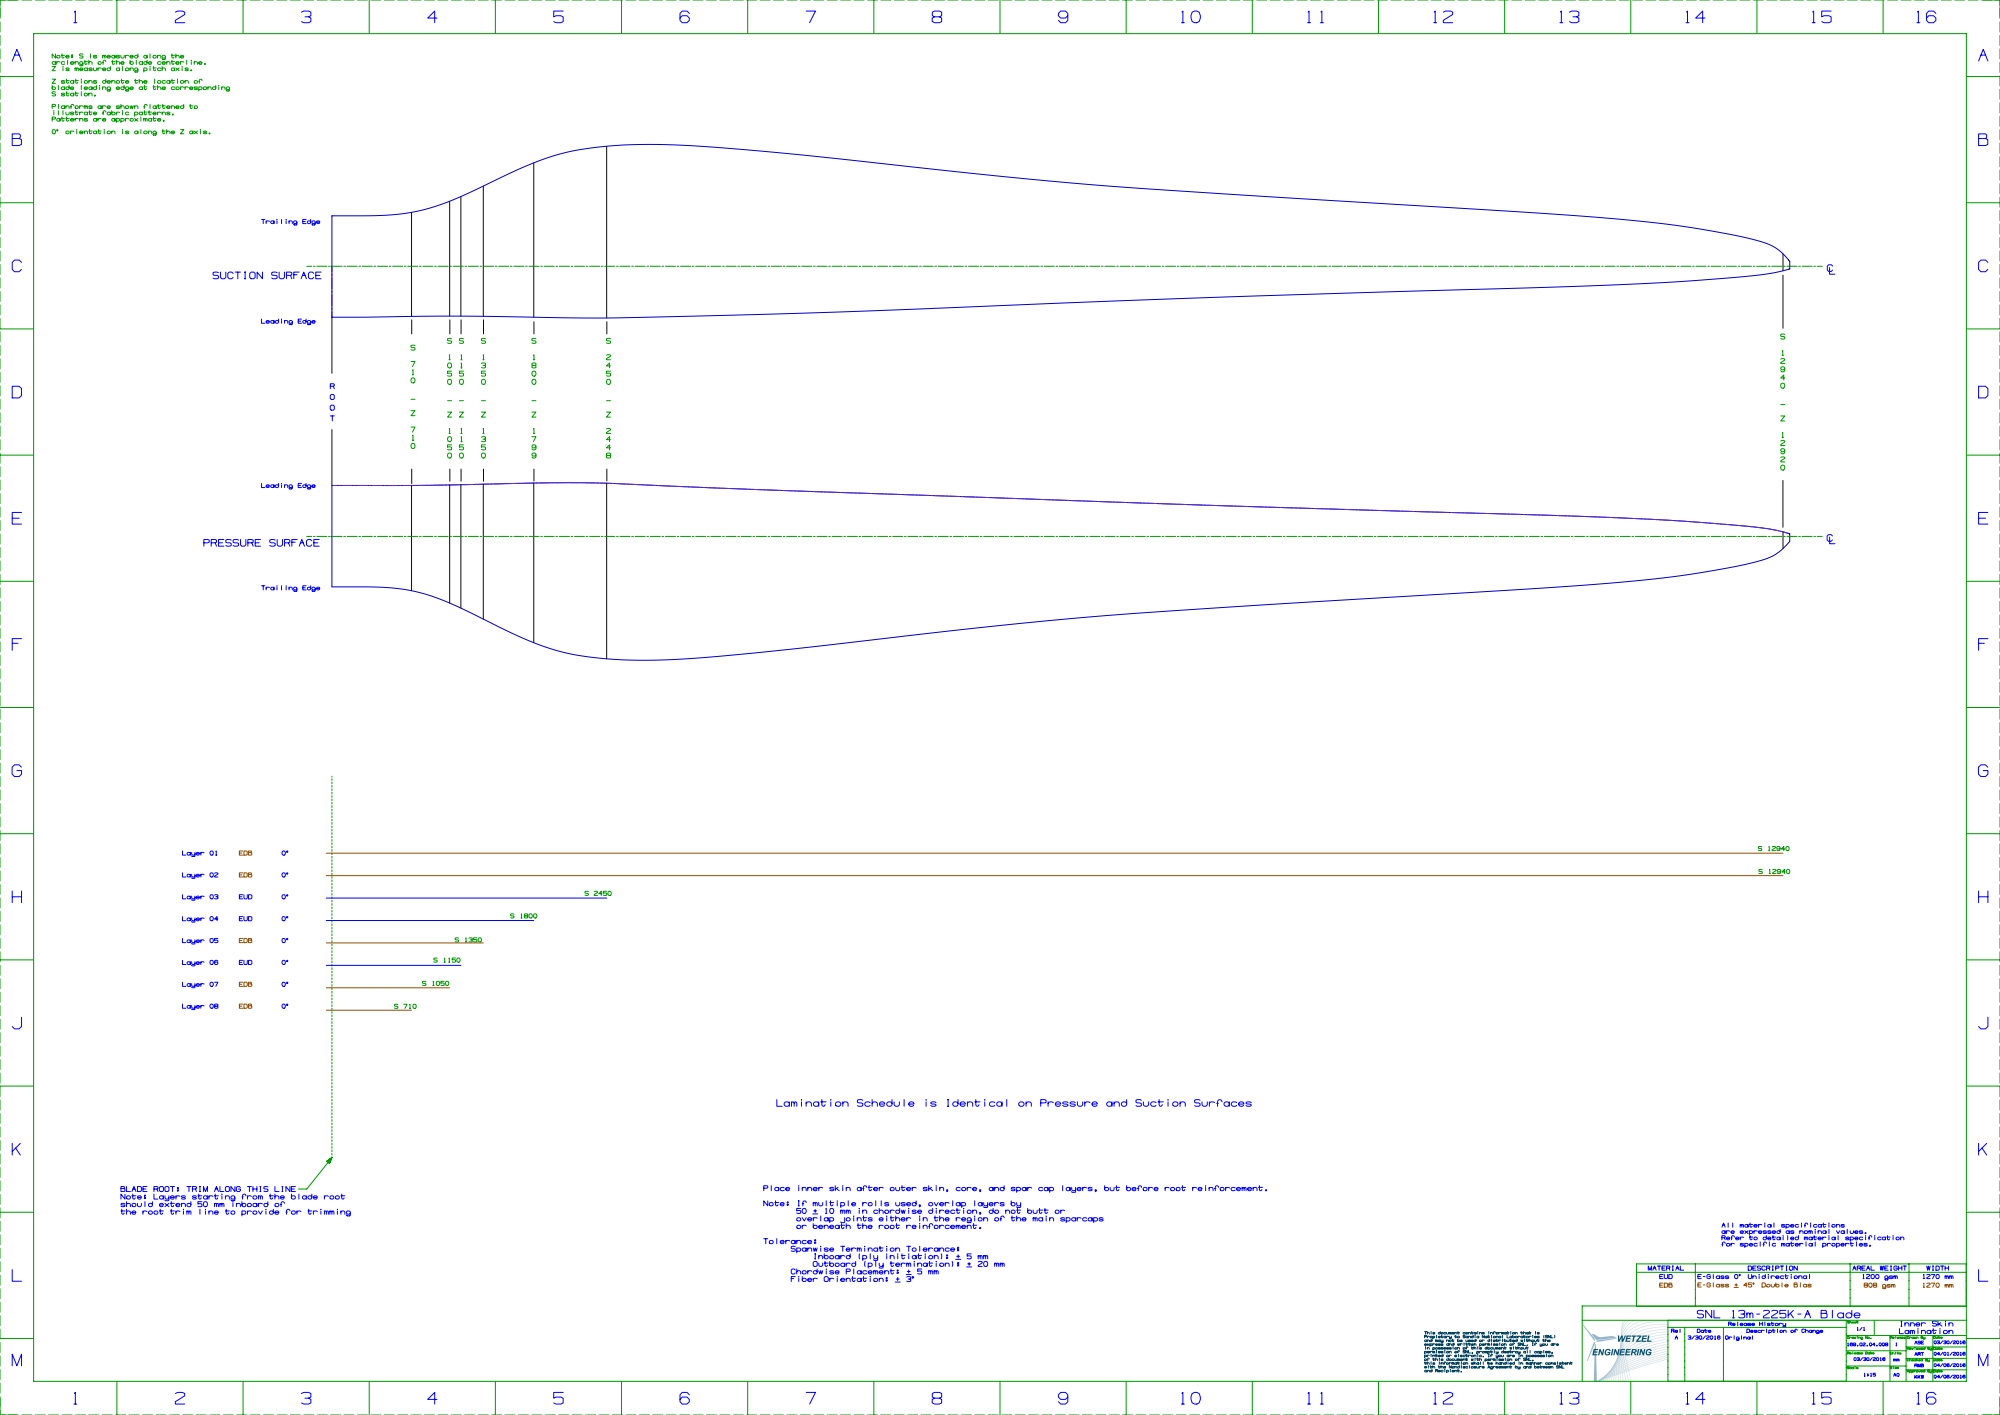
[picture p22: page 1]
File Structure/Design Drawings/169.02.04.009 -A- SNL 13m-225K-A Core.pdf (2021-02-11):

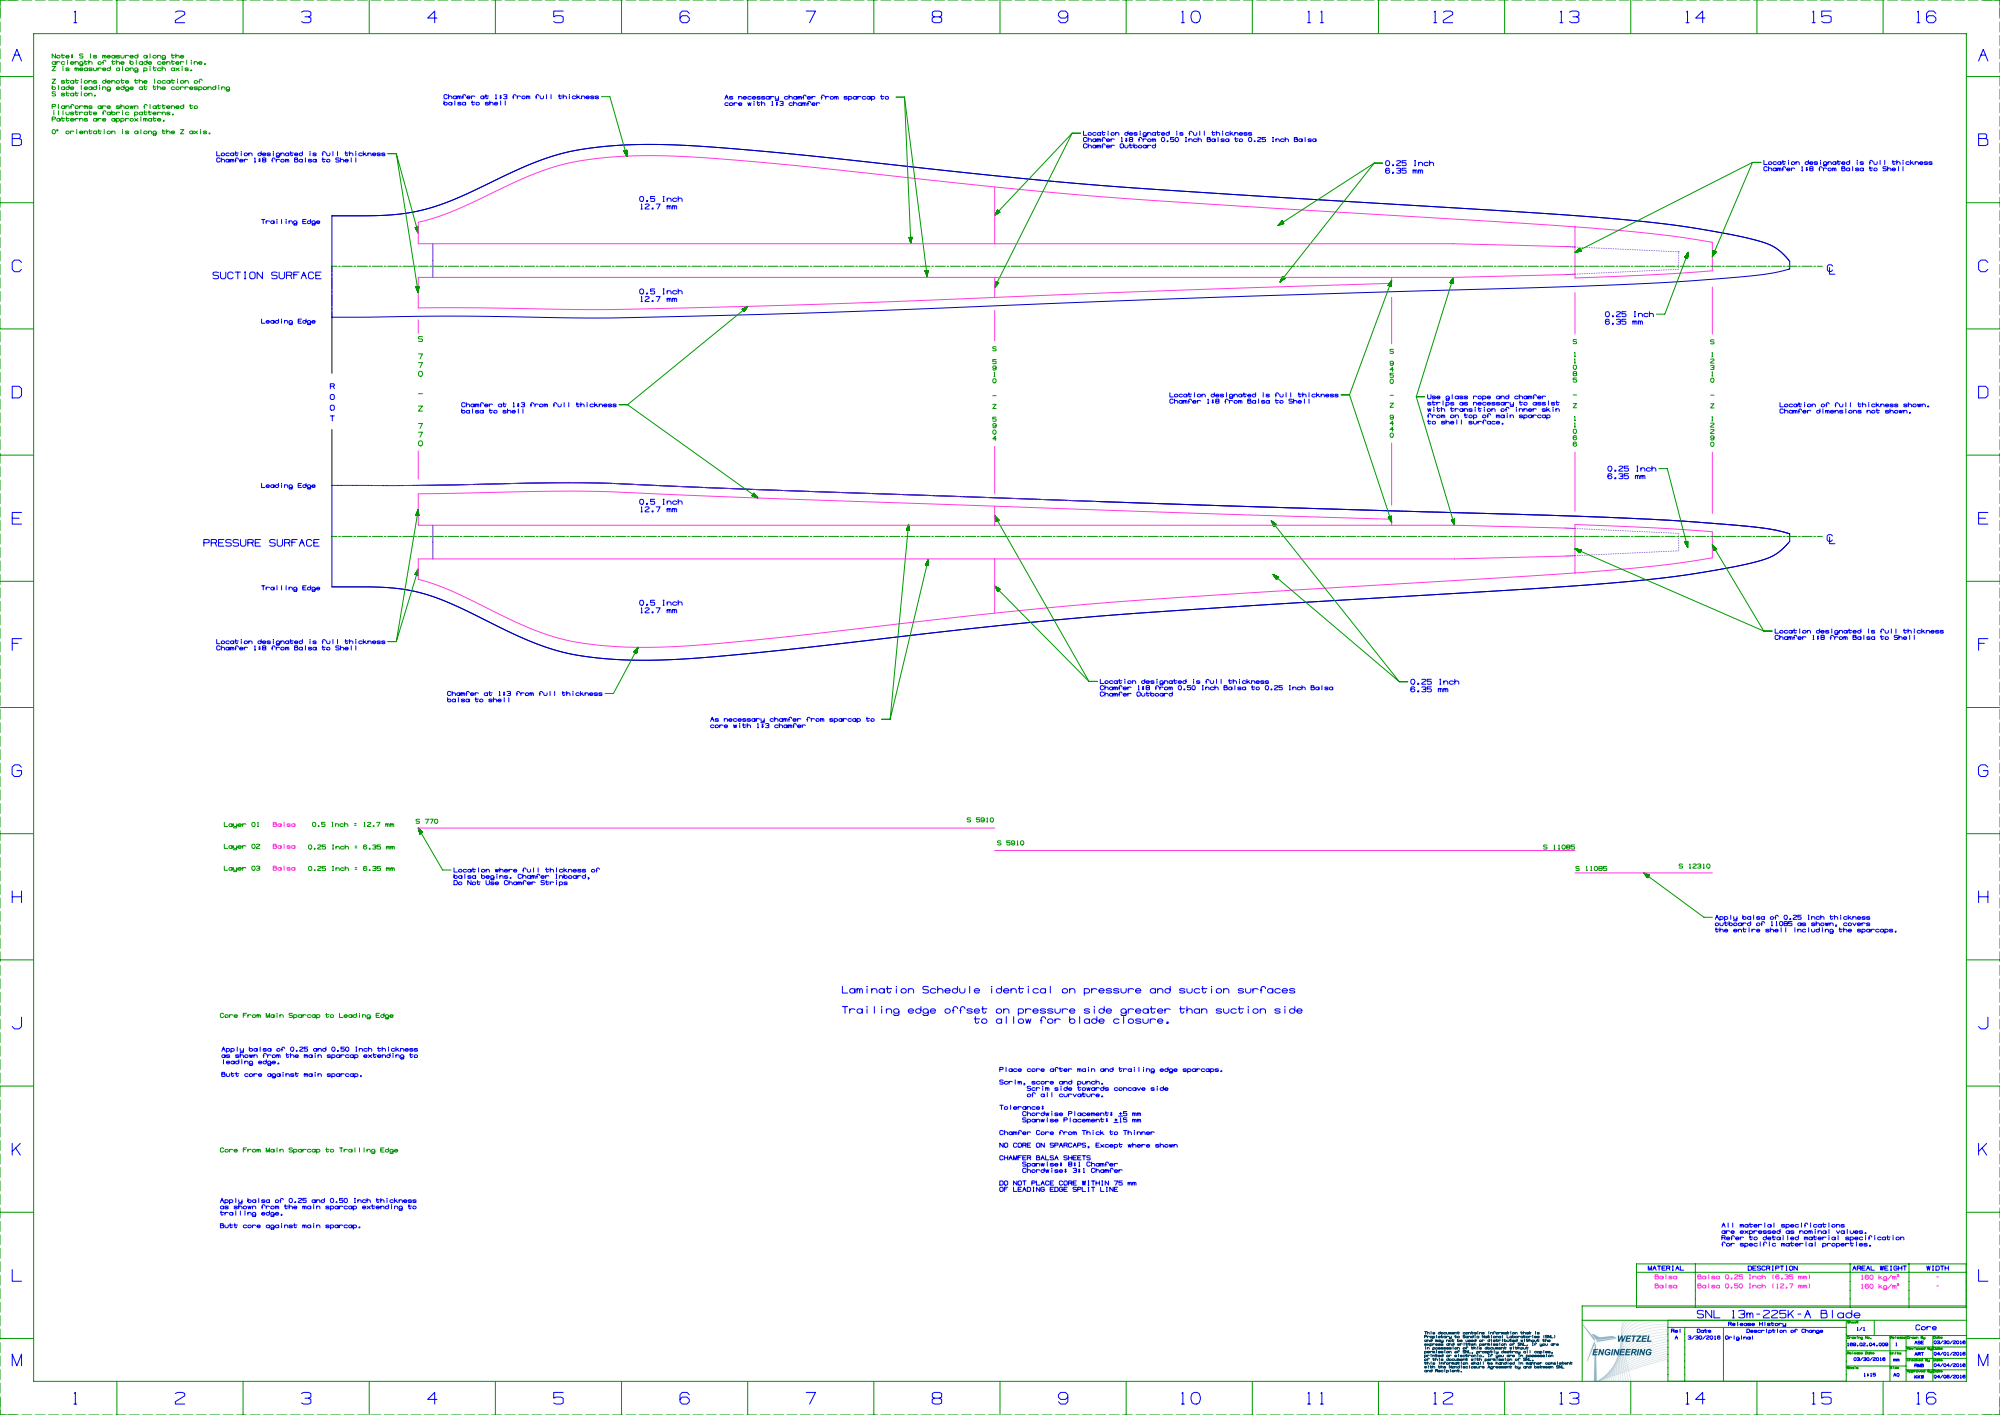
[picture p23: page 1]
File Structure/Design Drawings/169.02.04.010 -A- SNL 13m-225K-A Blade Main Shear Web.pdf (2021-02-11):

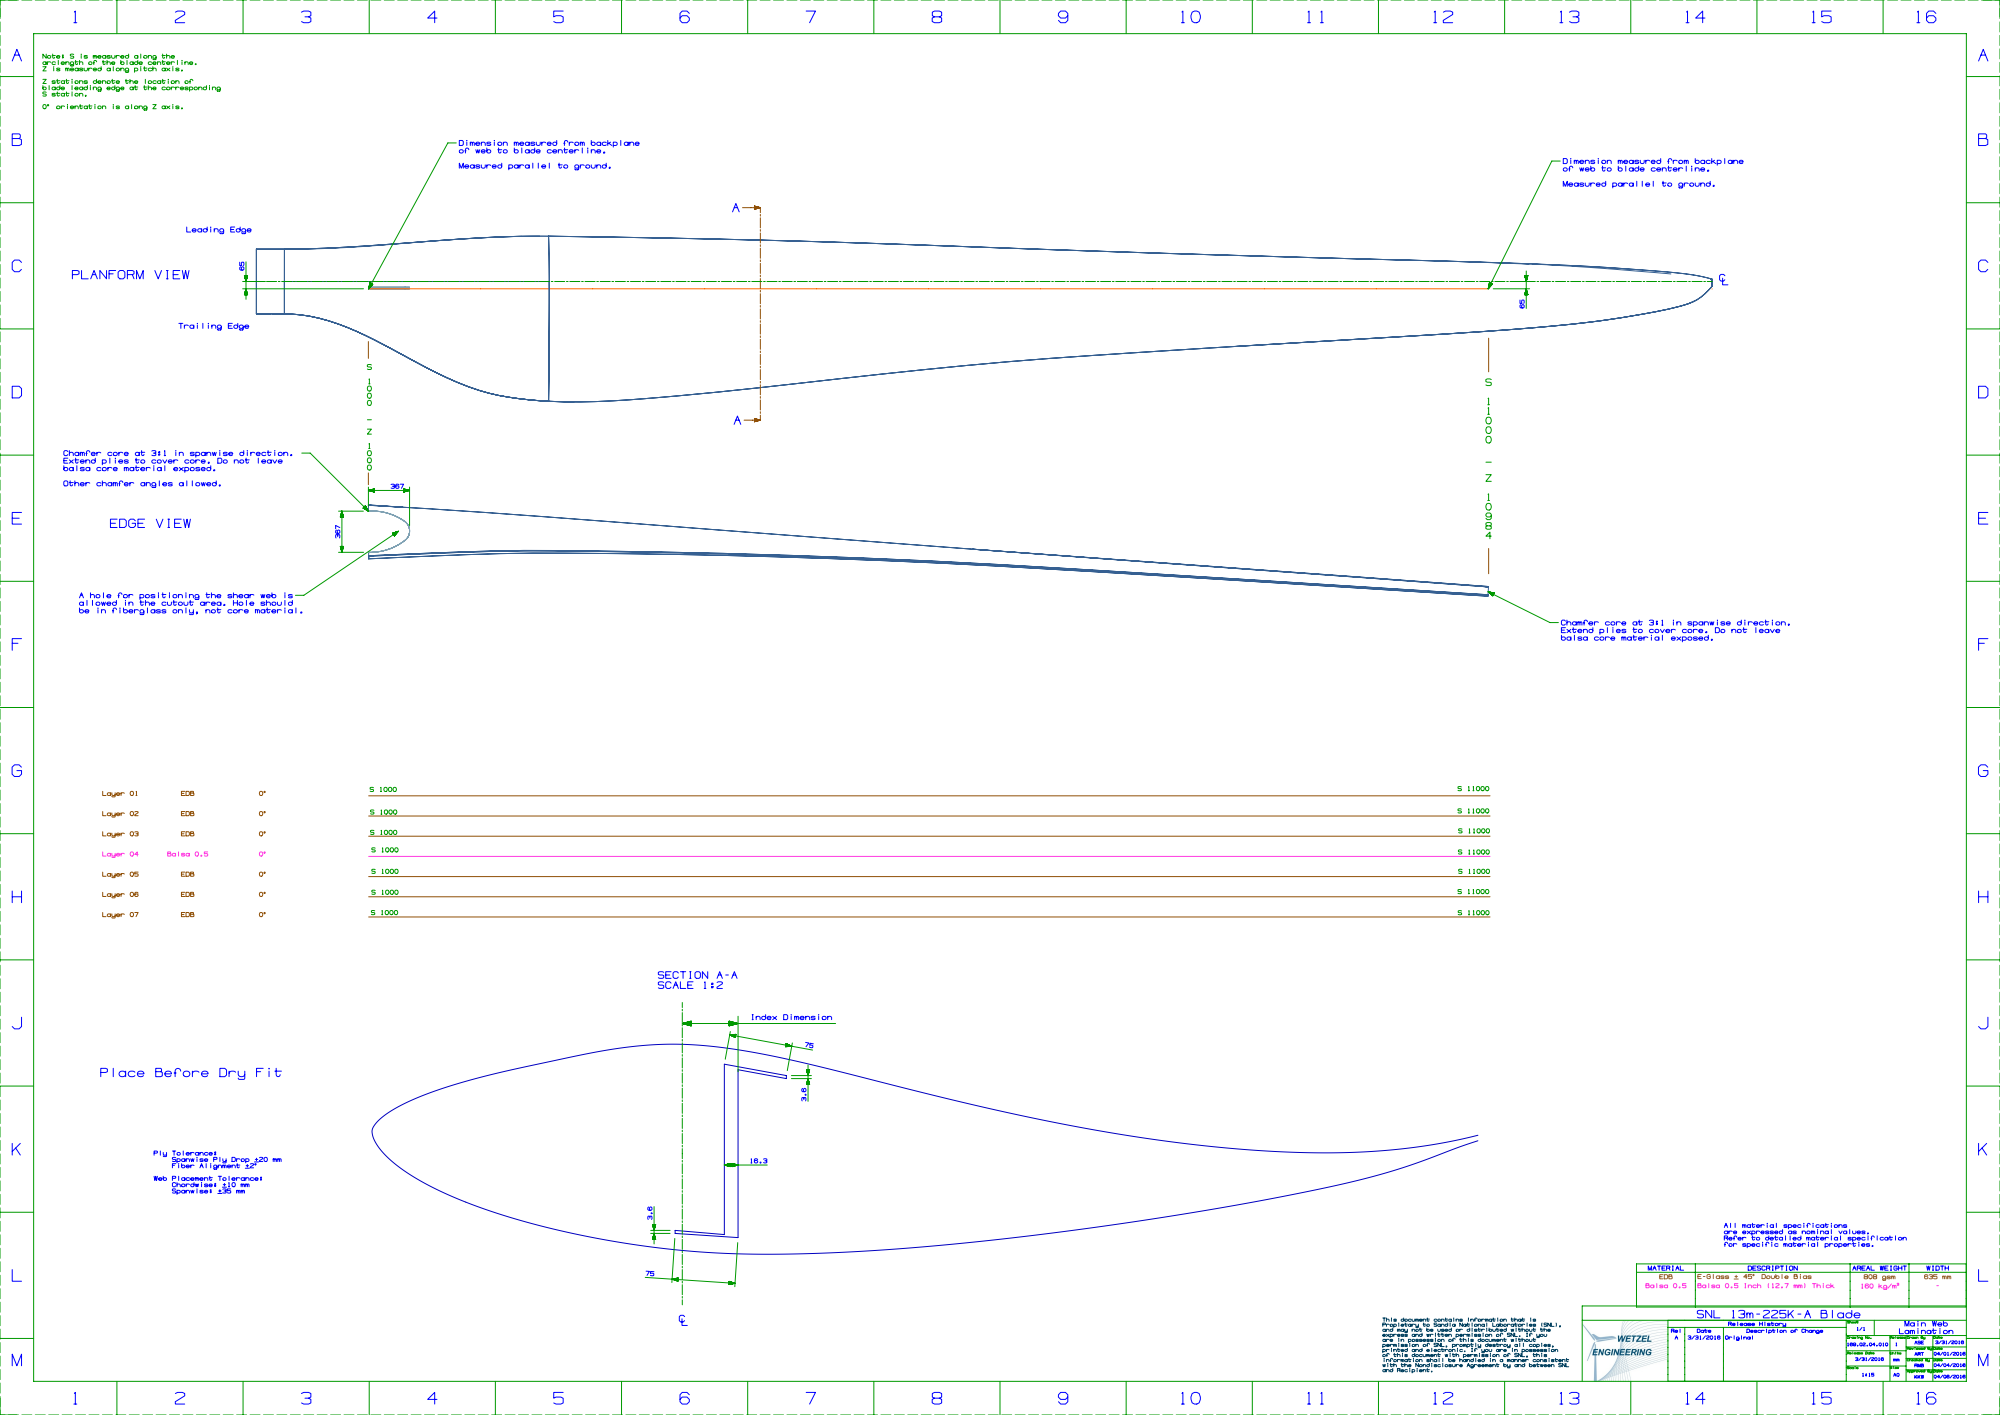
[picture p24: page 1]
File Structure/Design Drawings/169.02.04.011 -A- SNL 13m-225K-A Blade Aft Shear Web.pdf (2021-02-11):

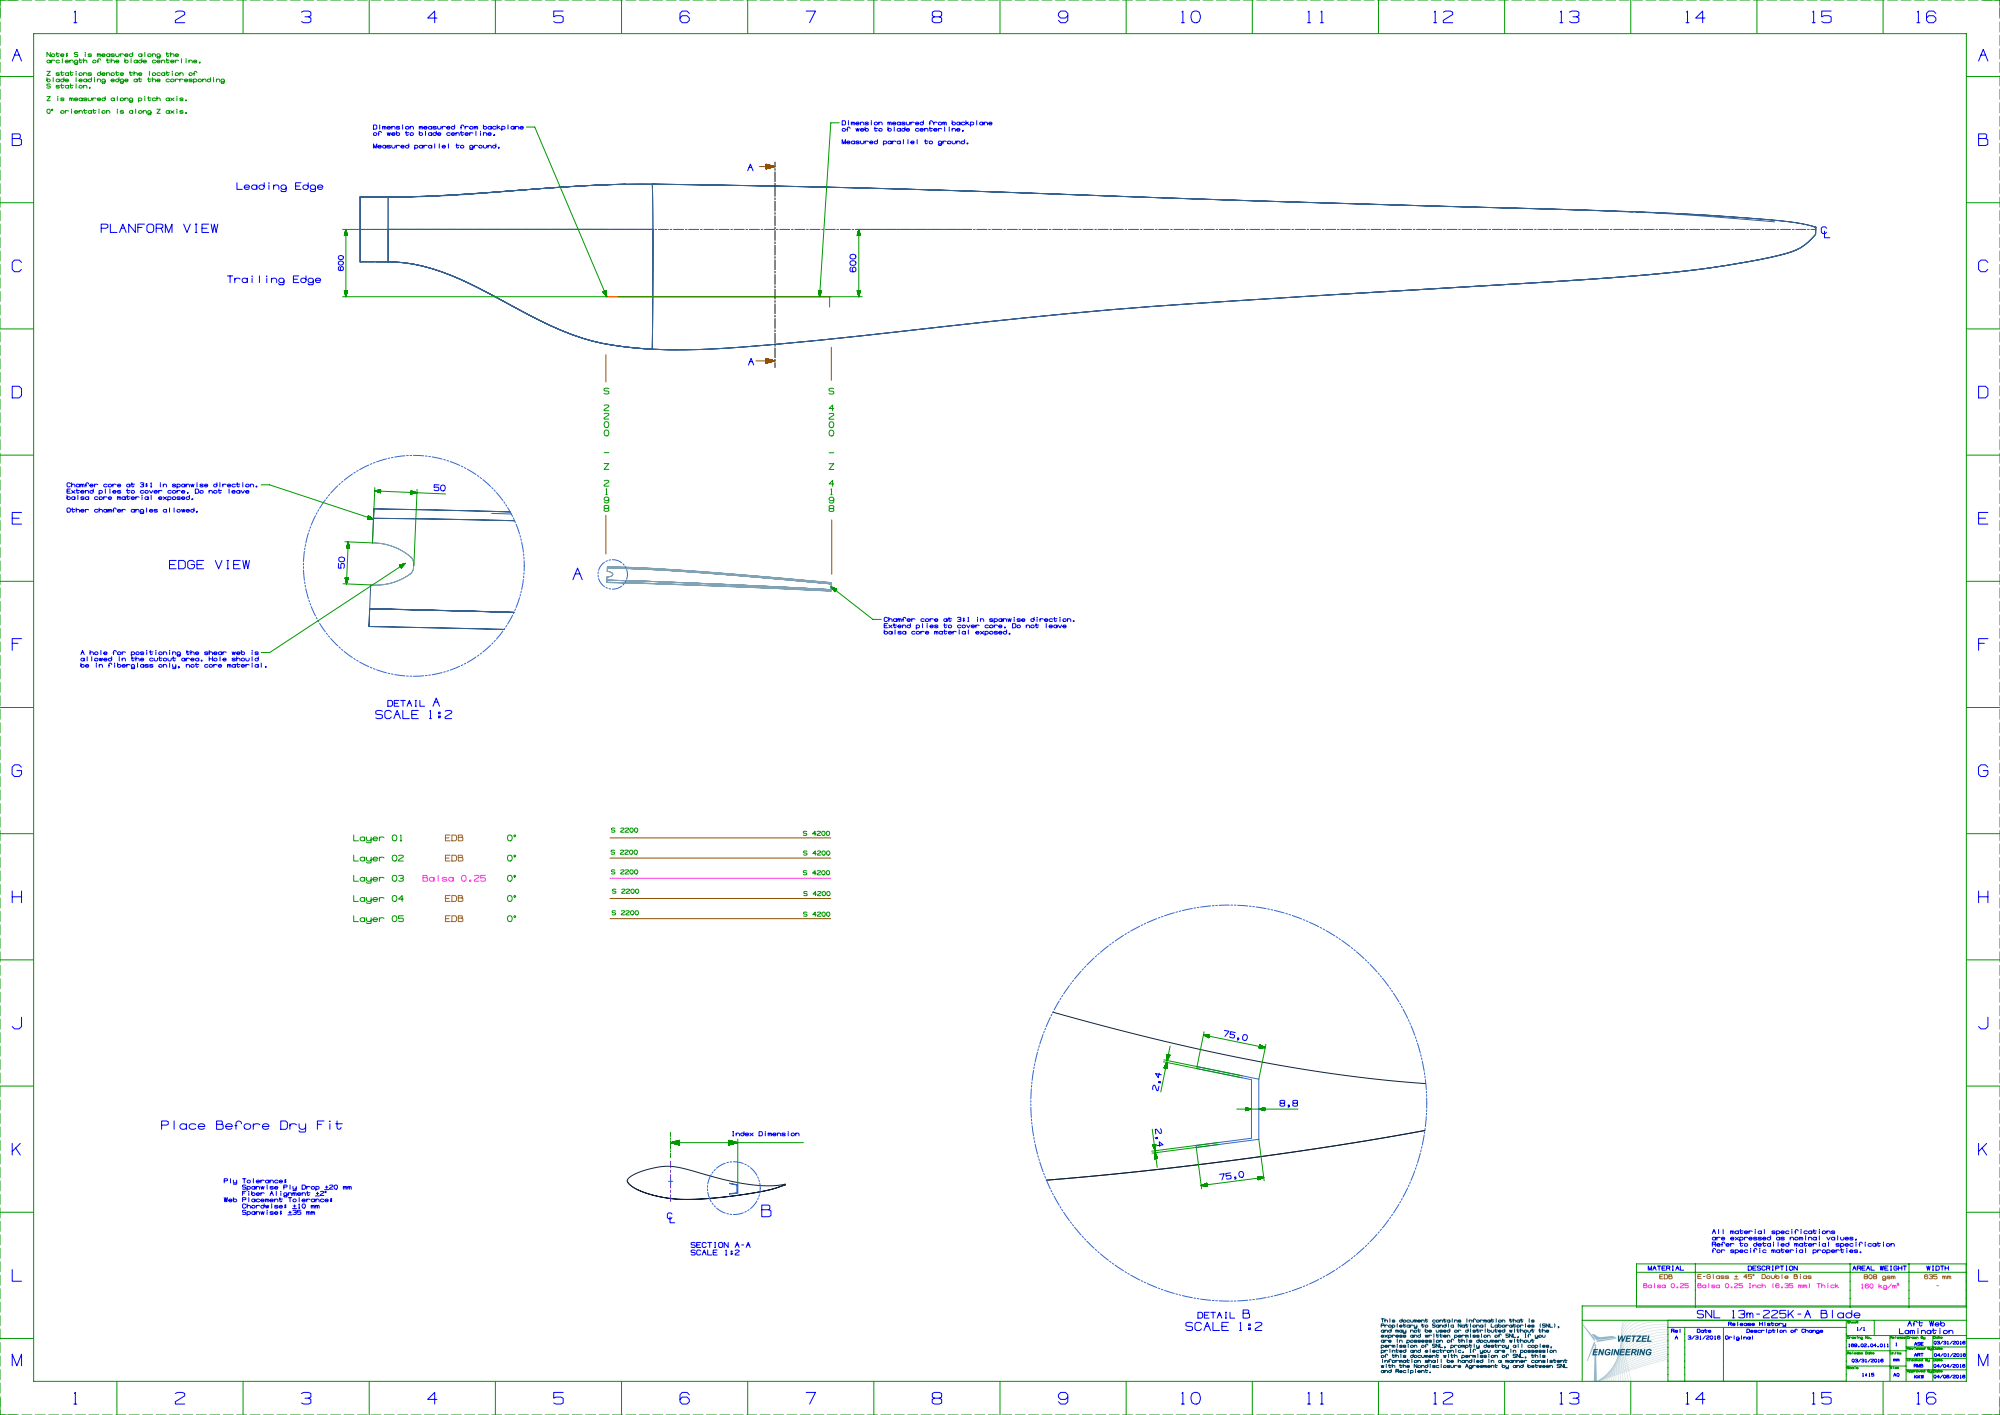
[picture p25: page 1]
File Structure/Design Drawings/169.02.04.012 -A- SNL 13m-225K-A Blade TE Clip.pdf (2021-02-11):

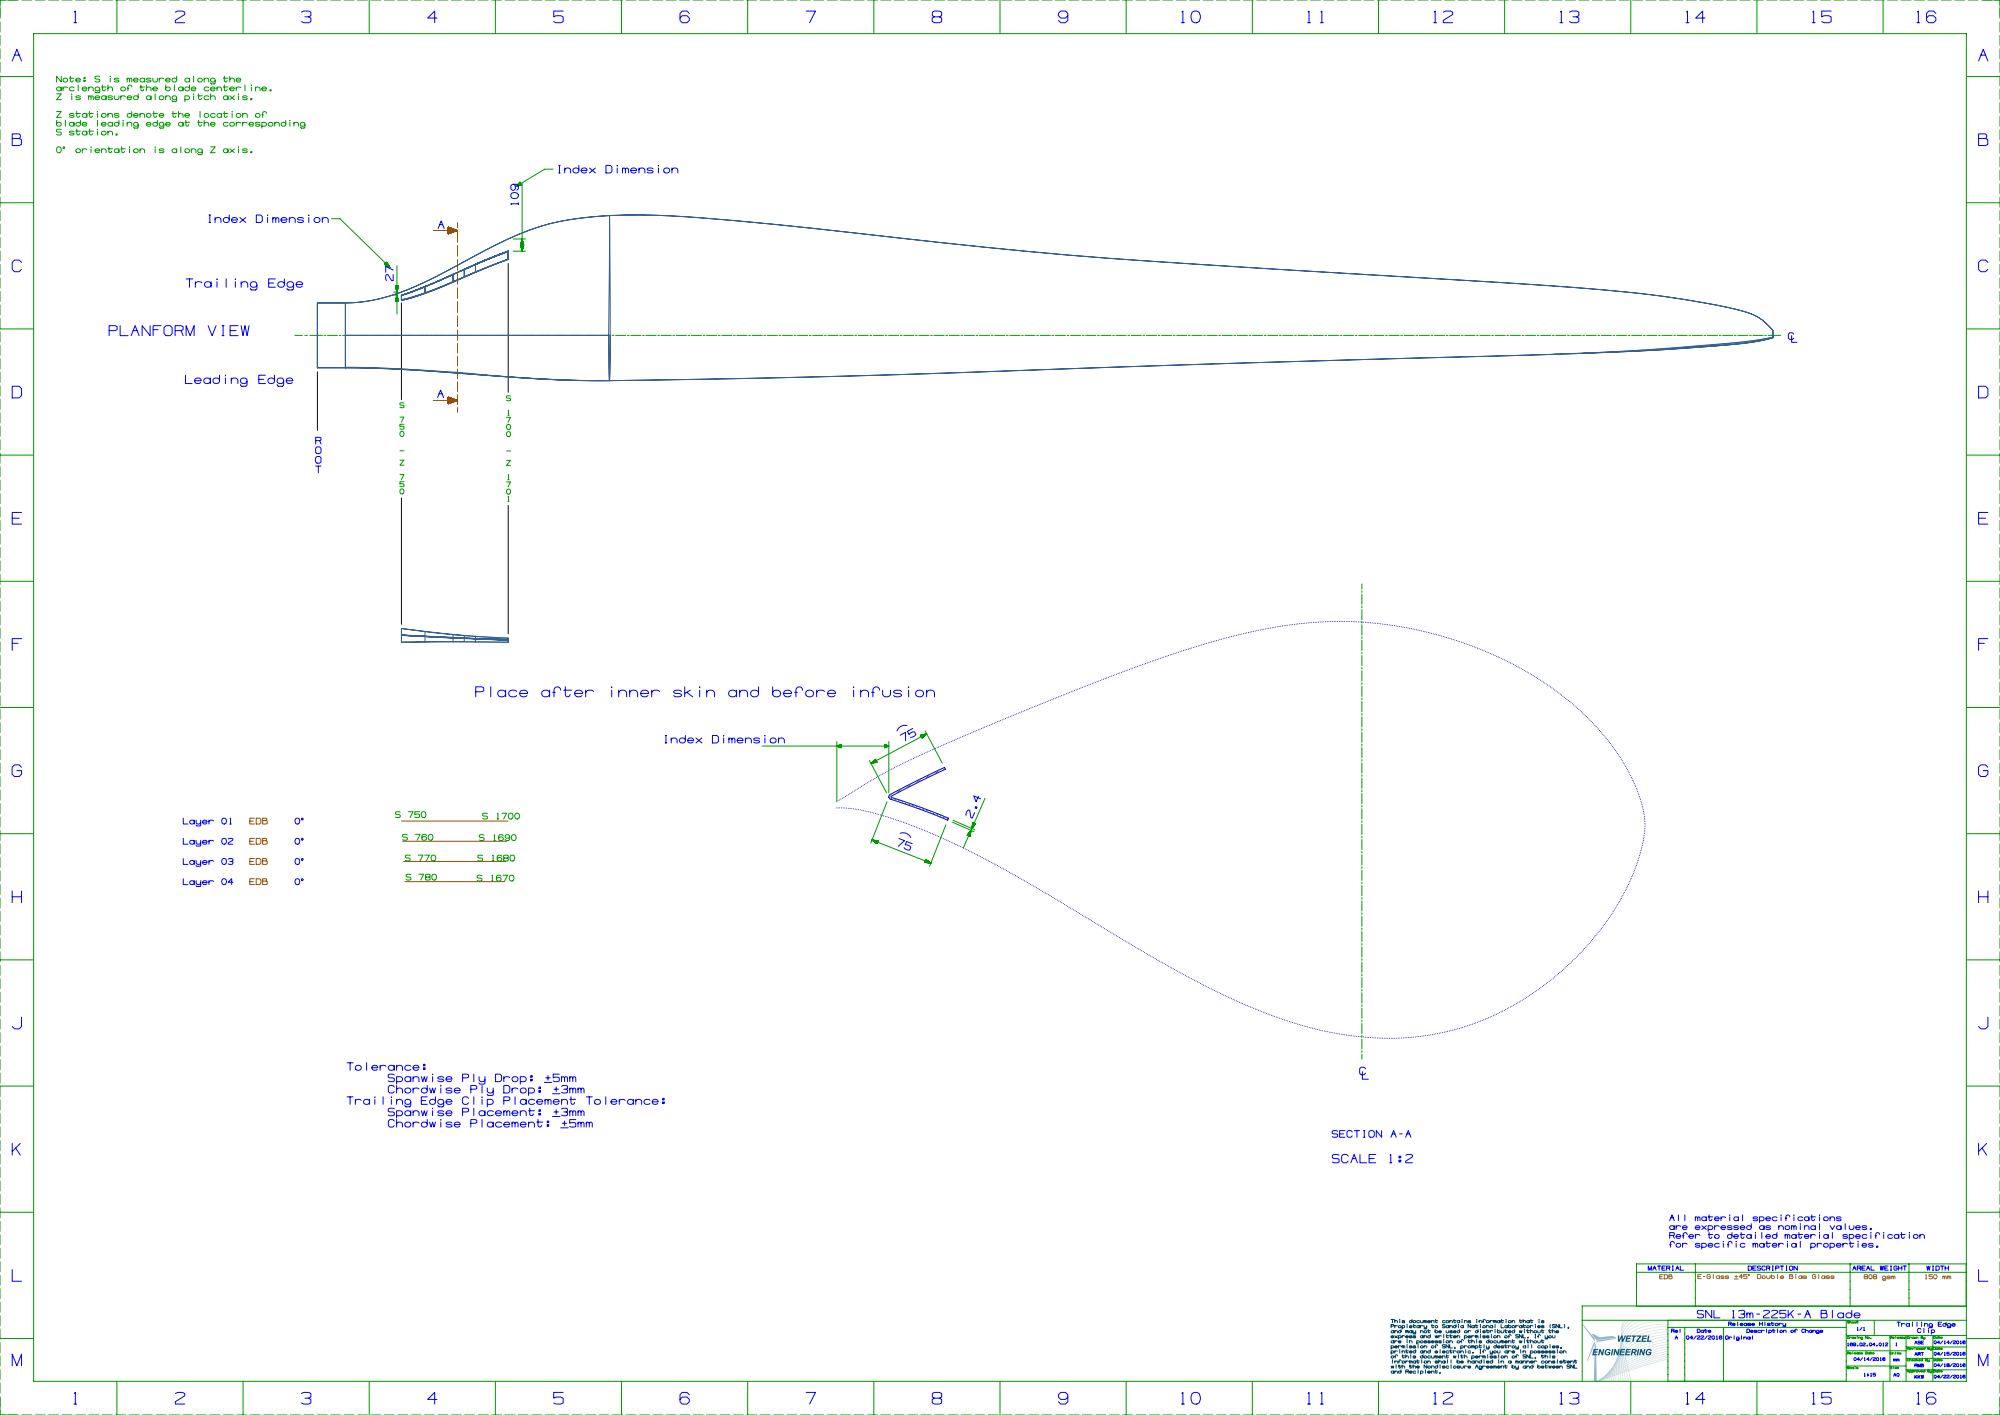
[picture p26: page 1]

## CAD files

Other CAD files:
FAST_v7/NRT_AD.ipt
FAST_v7/pitch.ipt
Structure/3D CAD Models/169.02.05.004 -A- SNL13m-225k-A Main Web Mold Surface.x_t
Structure/3D CAD Models/169.02.05.005 -A- SNL13m-225k-A Aft Web Mold Surface.x_t
Structure/3D CAD Models/169.02.05.006- A - SNL13m-225k-A Leading Edge Clip Mold Surface.x_t
Structure/3D CAD Models/169.02.05.007- A - SNL13m-225k-A Trailing Edge Clip Mold Surface.x_t
Structure/3D CAD Models/169.02.05.009 - A - SNL 13m-225k-A Blade Balance Box.x_t
